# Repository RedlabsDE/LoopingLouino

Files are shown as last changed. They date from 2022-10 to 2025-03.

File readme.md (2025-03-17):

# LoopingLouino Project

find pictures and further description here: https://redlabs.de/blog/looping-louino/

## Repository Overview
- **documentation**
  - pictures of this project
- **firmware**
  - Arduino Project
- **hardware**
  - **KiCAD** Project Folder including schematic, PCB layout and BOM
  - **schematic** and fabrication layer drawing as PDF
  - **datasheet** of used components
  
## Hardware
- Order PCB: https://aisler.net/p/MKIYMUSK
- Assemble PCB (find BOM in \hardware\schematic)
- Rework PCB as described in the schematic

## Firmware

### Flash Arduino bootloader to your Atmega328

1. Open Atmel Studio (now Microchip Studio)
2. Start the Tool Manager. Connec your Atmel ISP to your PC and to the PCB (CON2, ISP 6-pin).
3. Select Tool and Device. Apply & Read.
4. "Fuses": Set Fuses (according to picture "Arduino Fuses.pg"). Program fuses to Device.
5. "Memories": For Flash, select the "optiboot_atmega328.hex" file. Program&Verify.

... find pictures and data here: \firmware\Arduino Bootloader

### Upload the LoopingLouino Fimrware 

Prepare:
- Get an USB/UART converter
- Connect the UART to the PCB (Pinheader P1, or use the Audio Jack J1)

Upload:
1. Open the firmware folder in VSCode
2. Install the "PlatformIO IDE" extension
3. Open the folder "180223-094129-pro16MHzatmega328" with the extension
4. Build and Upload the project.

... find other projects: https://redlabs.de/

### Debug the Firmware

In main.cpp set "#define DEBUG 1" to get serial debug information (8n1 19200)

### Adaptions in the Firware

According to the used Supply Voltage, set: #define SPEED_CORRECTION_FACTOR (main.h)

According to the number of LEDs used, set: #define NUM_LEDS (LEDcntrl.h)

## Mechanics

//TODO: add pictures

Open all screws (short / long)

remove black cable (between motor and batteries)
remove red cable (between switch and batteries)
remove battery clips

add new black cable to motor (20cm)
add new red cable to switch (20cm)

cut through plastic (battery holder)
drill through plastic frame (for DC Jack, Button and optional RC-Jack)

cut digital LED strip and attach 3-wire ribbon cable (20LEDs, or other number)

solder 3-wire LED cable to PCB
solder 2-Wire Motor-and-Switch cable to PCB

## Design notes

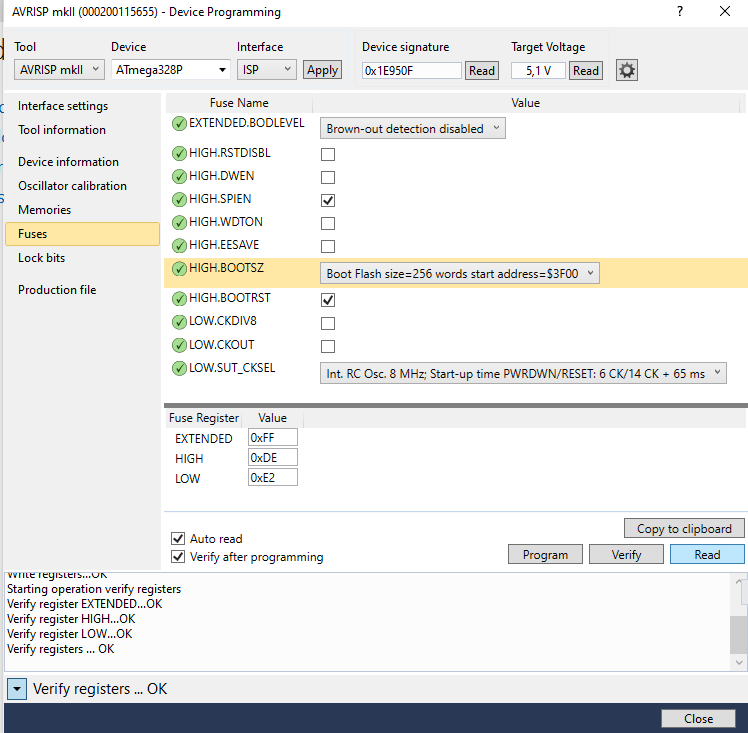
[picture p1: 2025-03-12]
firmware/Arduino Bootloader/Arduino Fuses.png

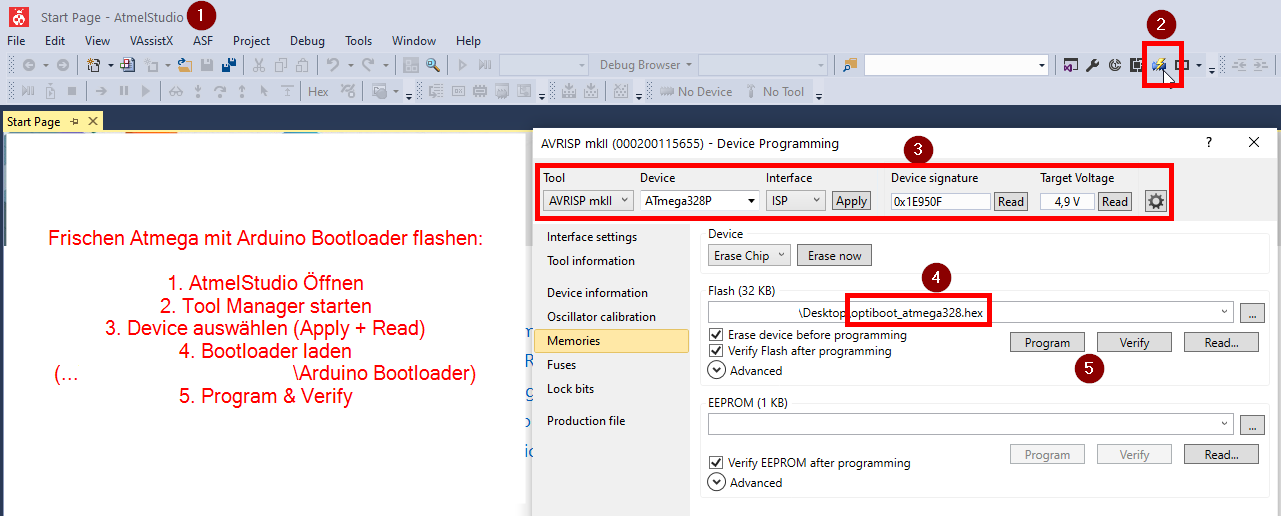
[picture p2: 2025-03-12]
firmware/Arduino Bootloader/Arduino Bootloader flashen.png

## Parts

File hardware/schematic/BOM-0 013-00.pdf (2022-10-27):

redlabs.de | BOM 013/00 | LoopingLouino
| | Total parts: | 50
v C | 22u | C_1206 | 1
C14 | 22u
v C | 100p | C_0603 | 1
C12 | 100p
v C | 1n | C_0603 | 4
C1 | 1n
C2 | 1n
C3 | 1n/200V
C4 | 1n
v C | 100n | C_0603 | 9
C5 | 100n
C6 | 100n
C7 | 100n
C8 | 100n
C10 | 100n/25V
C11 | 100n
C17 | 100n
C18 | 100n
C19 | 100n
v C | 1u/25V | C_0805 | 2
C9 | 1u/25V
C16 | 1u/25V
v R | 2R2 | R_0805 | 1
R17 | 2R2
v R | 1k | R_0603 | 3
R3 | 1k
R21 | 1k
R22 | 1k
v R | 4k7 | R_0603 | 2
R9 | 4k7
R10 | 4k7
v R | 7k5 | R_0603 | 1
R16 | 7k5
v R | 10k | R_0603 | 6
R1 | 10k
R13 | 10k
R14 | 10k
R18 | 10k
R19 | 10k
R20 | 10k
v R | 22k | R_0603 | 3
R2 | 22k
R23 | 22k
R24 | 22k
v R | 39k | R_0603 | 1
R15 | 39k
v R | 100k | R_0603 | 3

R7 | 100k
R8 | 100k
R12 | 100k
v D | SK34A | D_SMA | 2
D1 | SK34A
D2 | SK34A
v L | 10uH | D_SMA | 1
L1 | 10uH (HPI0530-100)
v Q | BCR141 | SOT-23 | 2
Q4 | BCR141
Q5 | BCR141
v IC | | | 3
IC1 | ATMEGA328P-A | TQFP-32_7x7mm_Pitch0.8mm
U2 | MP1584 | SO8N
U3 | ZXMHC6A07T8-2 | SOT-223-8
v SW | Switches | | 2
SW1 | SW_PUSH | SW_Tactile_SPST_Angled_PTS645Vx83-2LFS
SW2 | SW_PUSH | SMD_pushbutton_4x6mm
v CON | Connectors | | 3
J1 | JACK_4P | Klinkenbuchse-1503-13VP3
CON1 | BARREL_JACK_reduced | BARREL_JACK_reduced
CON2 | AVR-ISP-6 | MicroMatch_2x3_SMD
v P | Pin Array
P2 | CONN_01X03 | PIN_ARRAY_3x1_drill_0.8mm
P3 | CONN_01X02 | JST_XH2P_oval_pads
v P | Not Populated | | 5
R11 | 33R | R_0603
R4 | 0R | R_0603
R5 | 10k | R_0603
R25 | 1k | R_0603
Q1 | PMV250 | SOT-23

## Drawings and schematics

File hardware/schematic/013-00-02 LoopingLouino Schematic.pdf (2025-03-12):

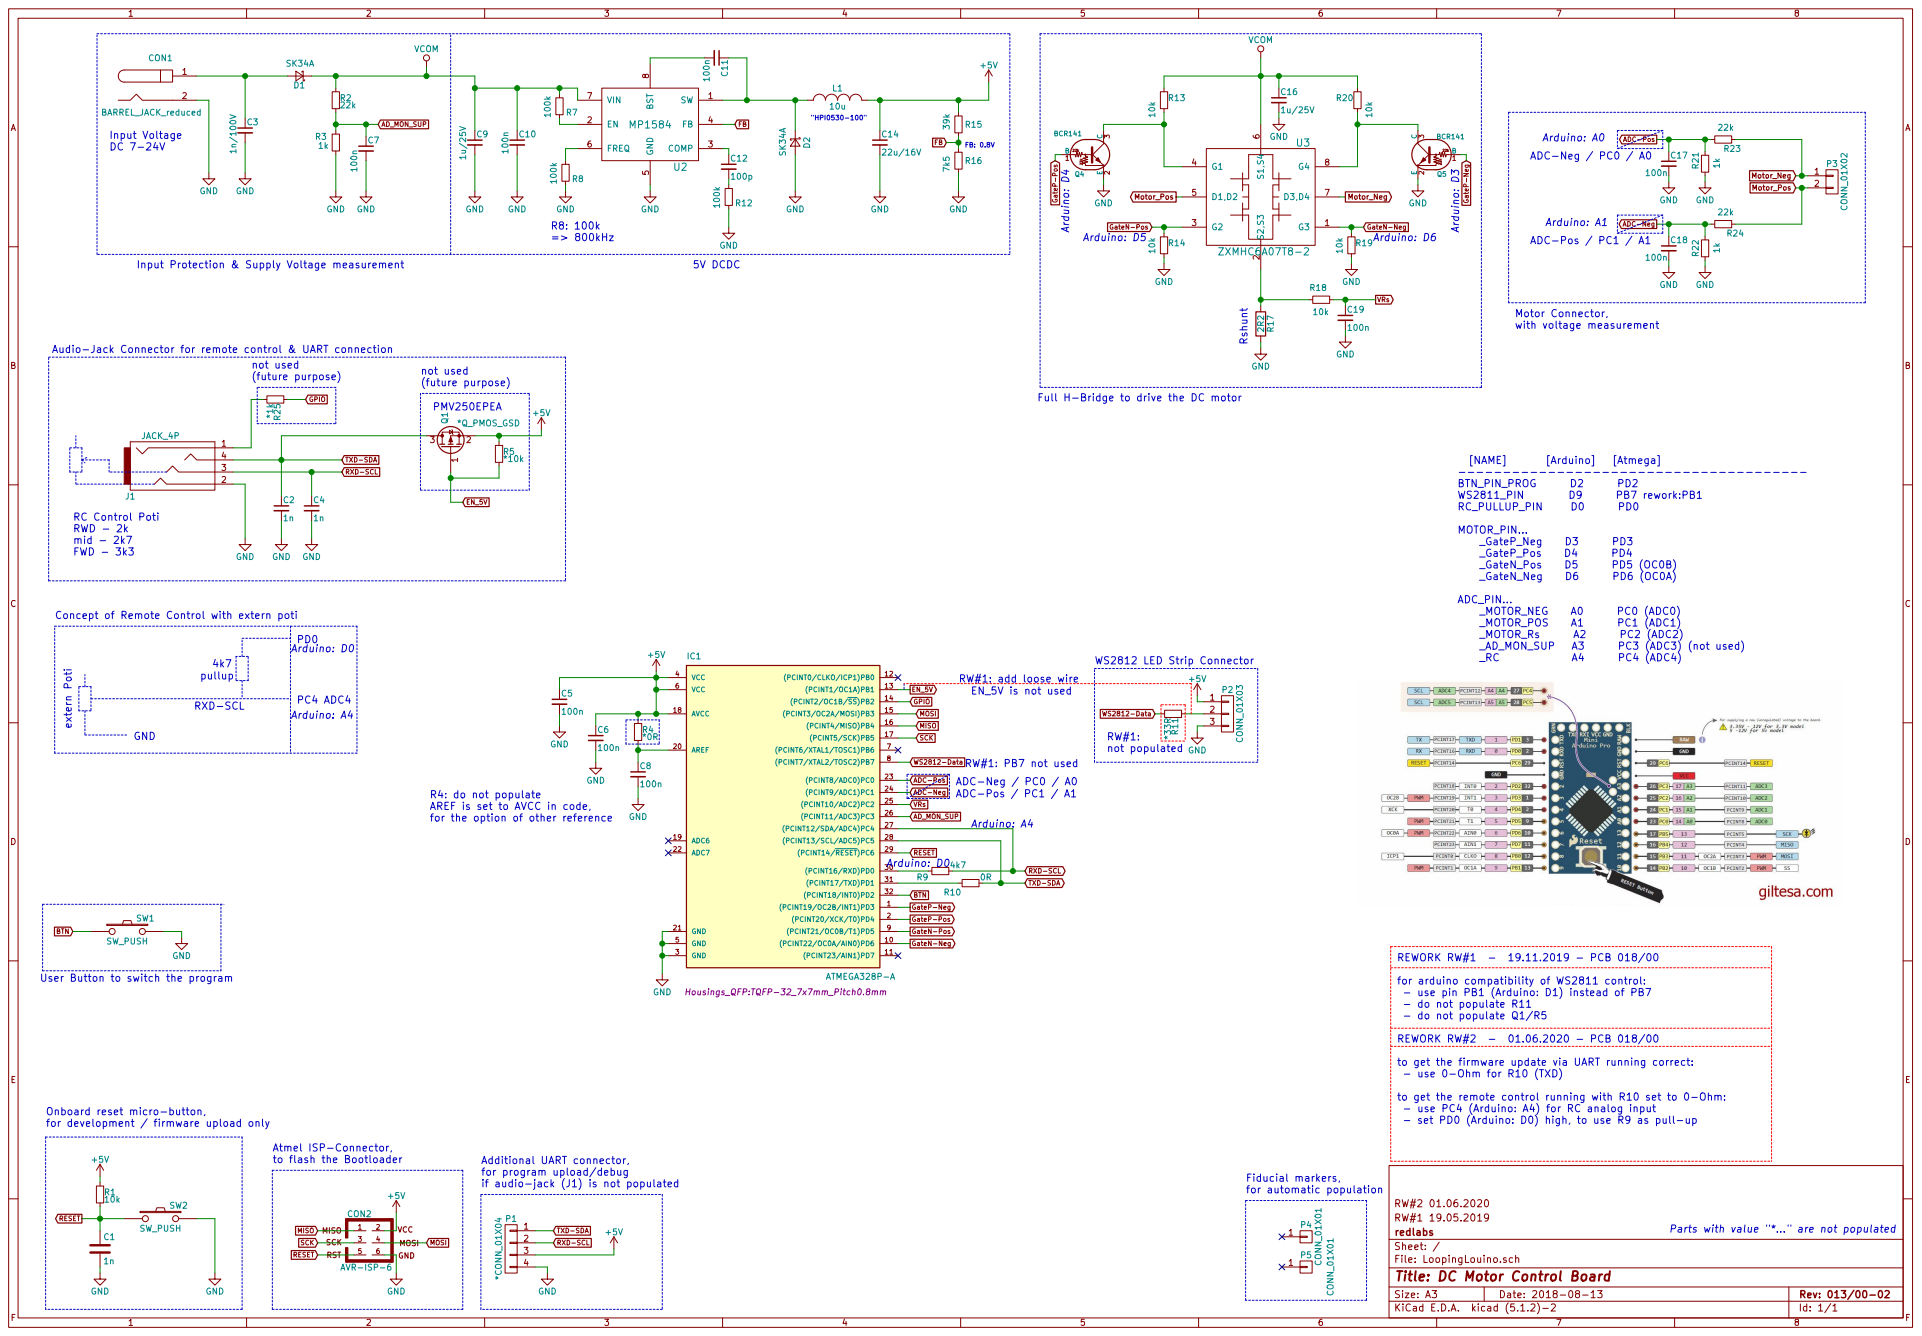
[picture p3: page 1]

Audio-Jack Connector for remote control & UART connection
Concept of Remote Control with extern poti not used

Full H-Bridge to drive the DC motor

RXD-SCL TXD-SDA

R4: do not populate
AREF is set to AVCC in code,
for the option of other reference

BTN
GateN-Pos GateN-Neg GateP-Pos GateP-Neg

User Button to switch the program

for arduino compatibility of WS2811 control:
- use pin PB1 (Arduino: D1) instead of PB7
- do not populate R11
- do not populate Q1/R5

to get the firmware update via UART running correct:
- use 0-Ohm for R10 (TXD)

to get the remote control running with R10 set to 0-Ohm:
- use PC4 (Arduino: A4) for RC analog input
- set PD0 (Arduino: D0) high, to use R9 as pull-up

Onboard reset micro-button,
for development / firmware upload only

Additional UART connector,
for program upload/debug
if audio-jack (J1) is not populated

File: LoopingLouino.sch Sheet: / redlabs RW#1 19.05.2019 RW#2 01.06.2020

Parts with value "*..." are not populated

Id: 1/1 Title: DC Motor Control Board

GND

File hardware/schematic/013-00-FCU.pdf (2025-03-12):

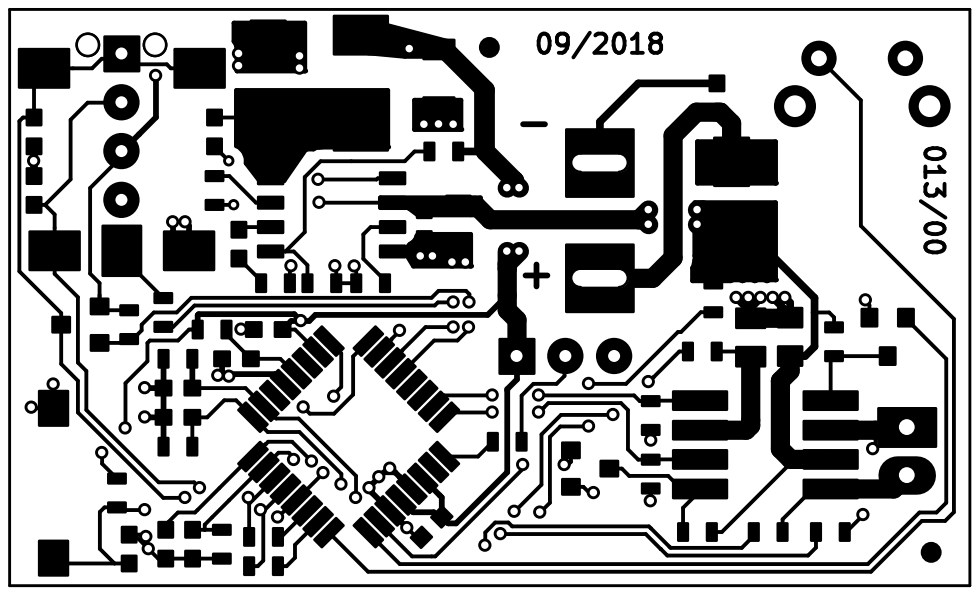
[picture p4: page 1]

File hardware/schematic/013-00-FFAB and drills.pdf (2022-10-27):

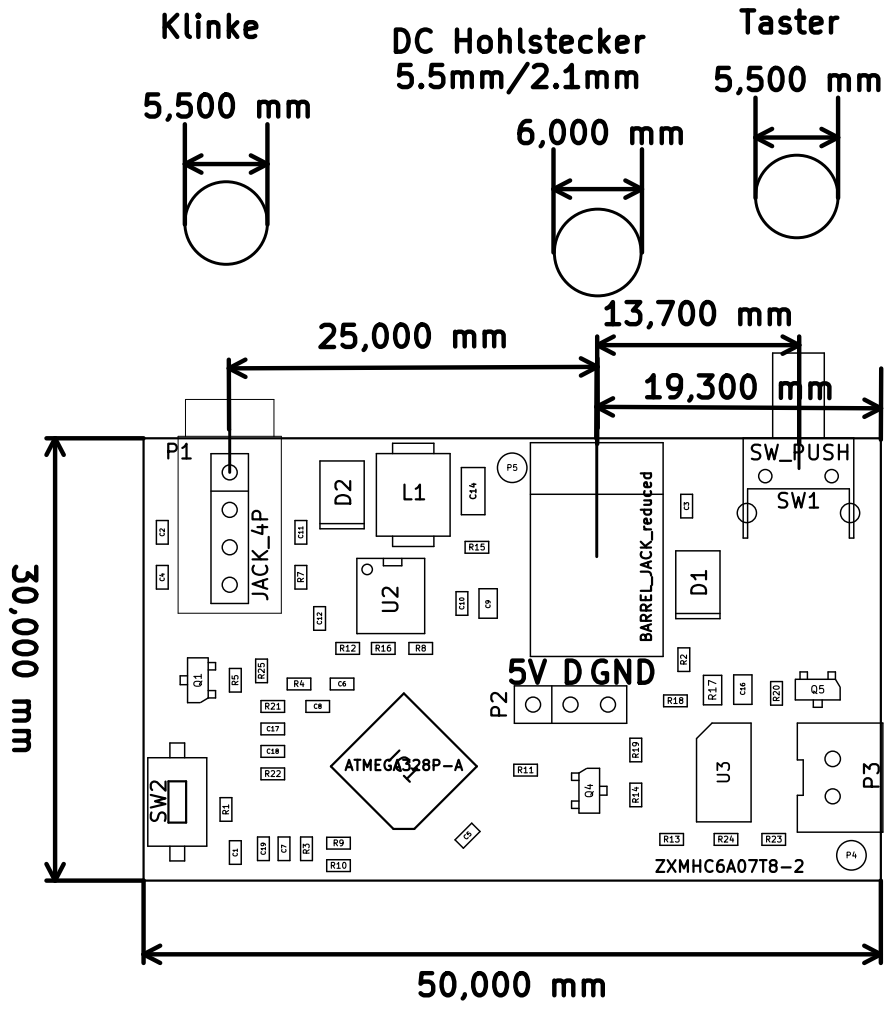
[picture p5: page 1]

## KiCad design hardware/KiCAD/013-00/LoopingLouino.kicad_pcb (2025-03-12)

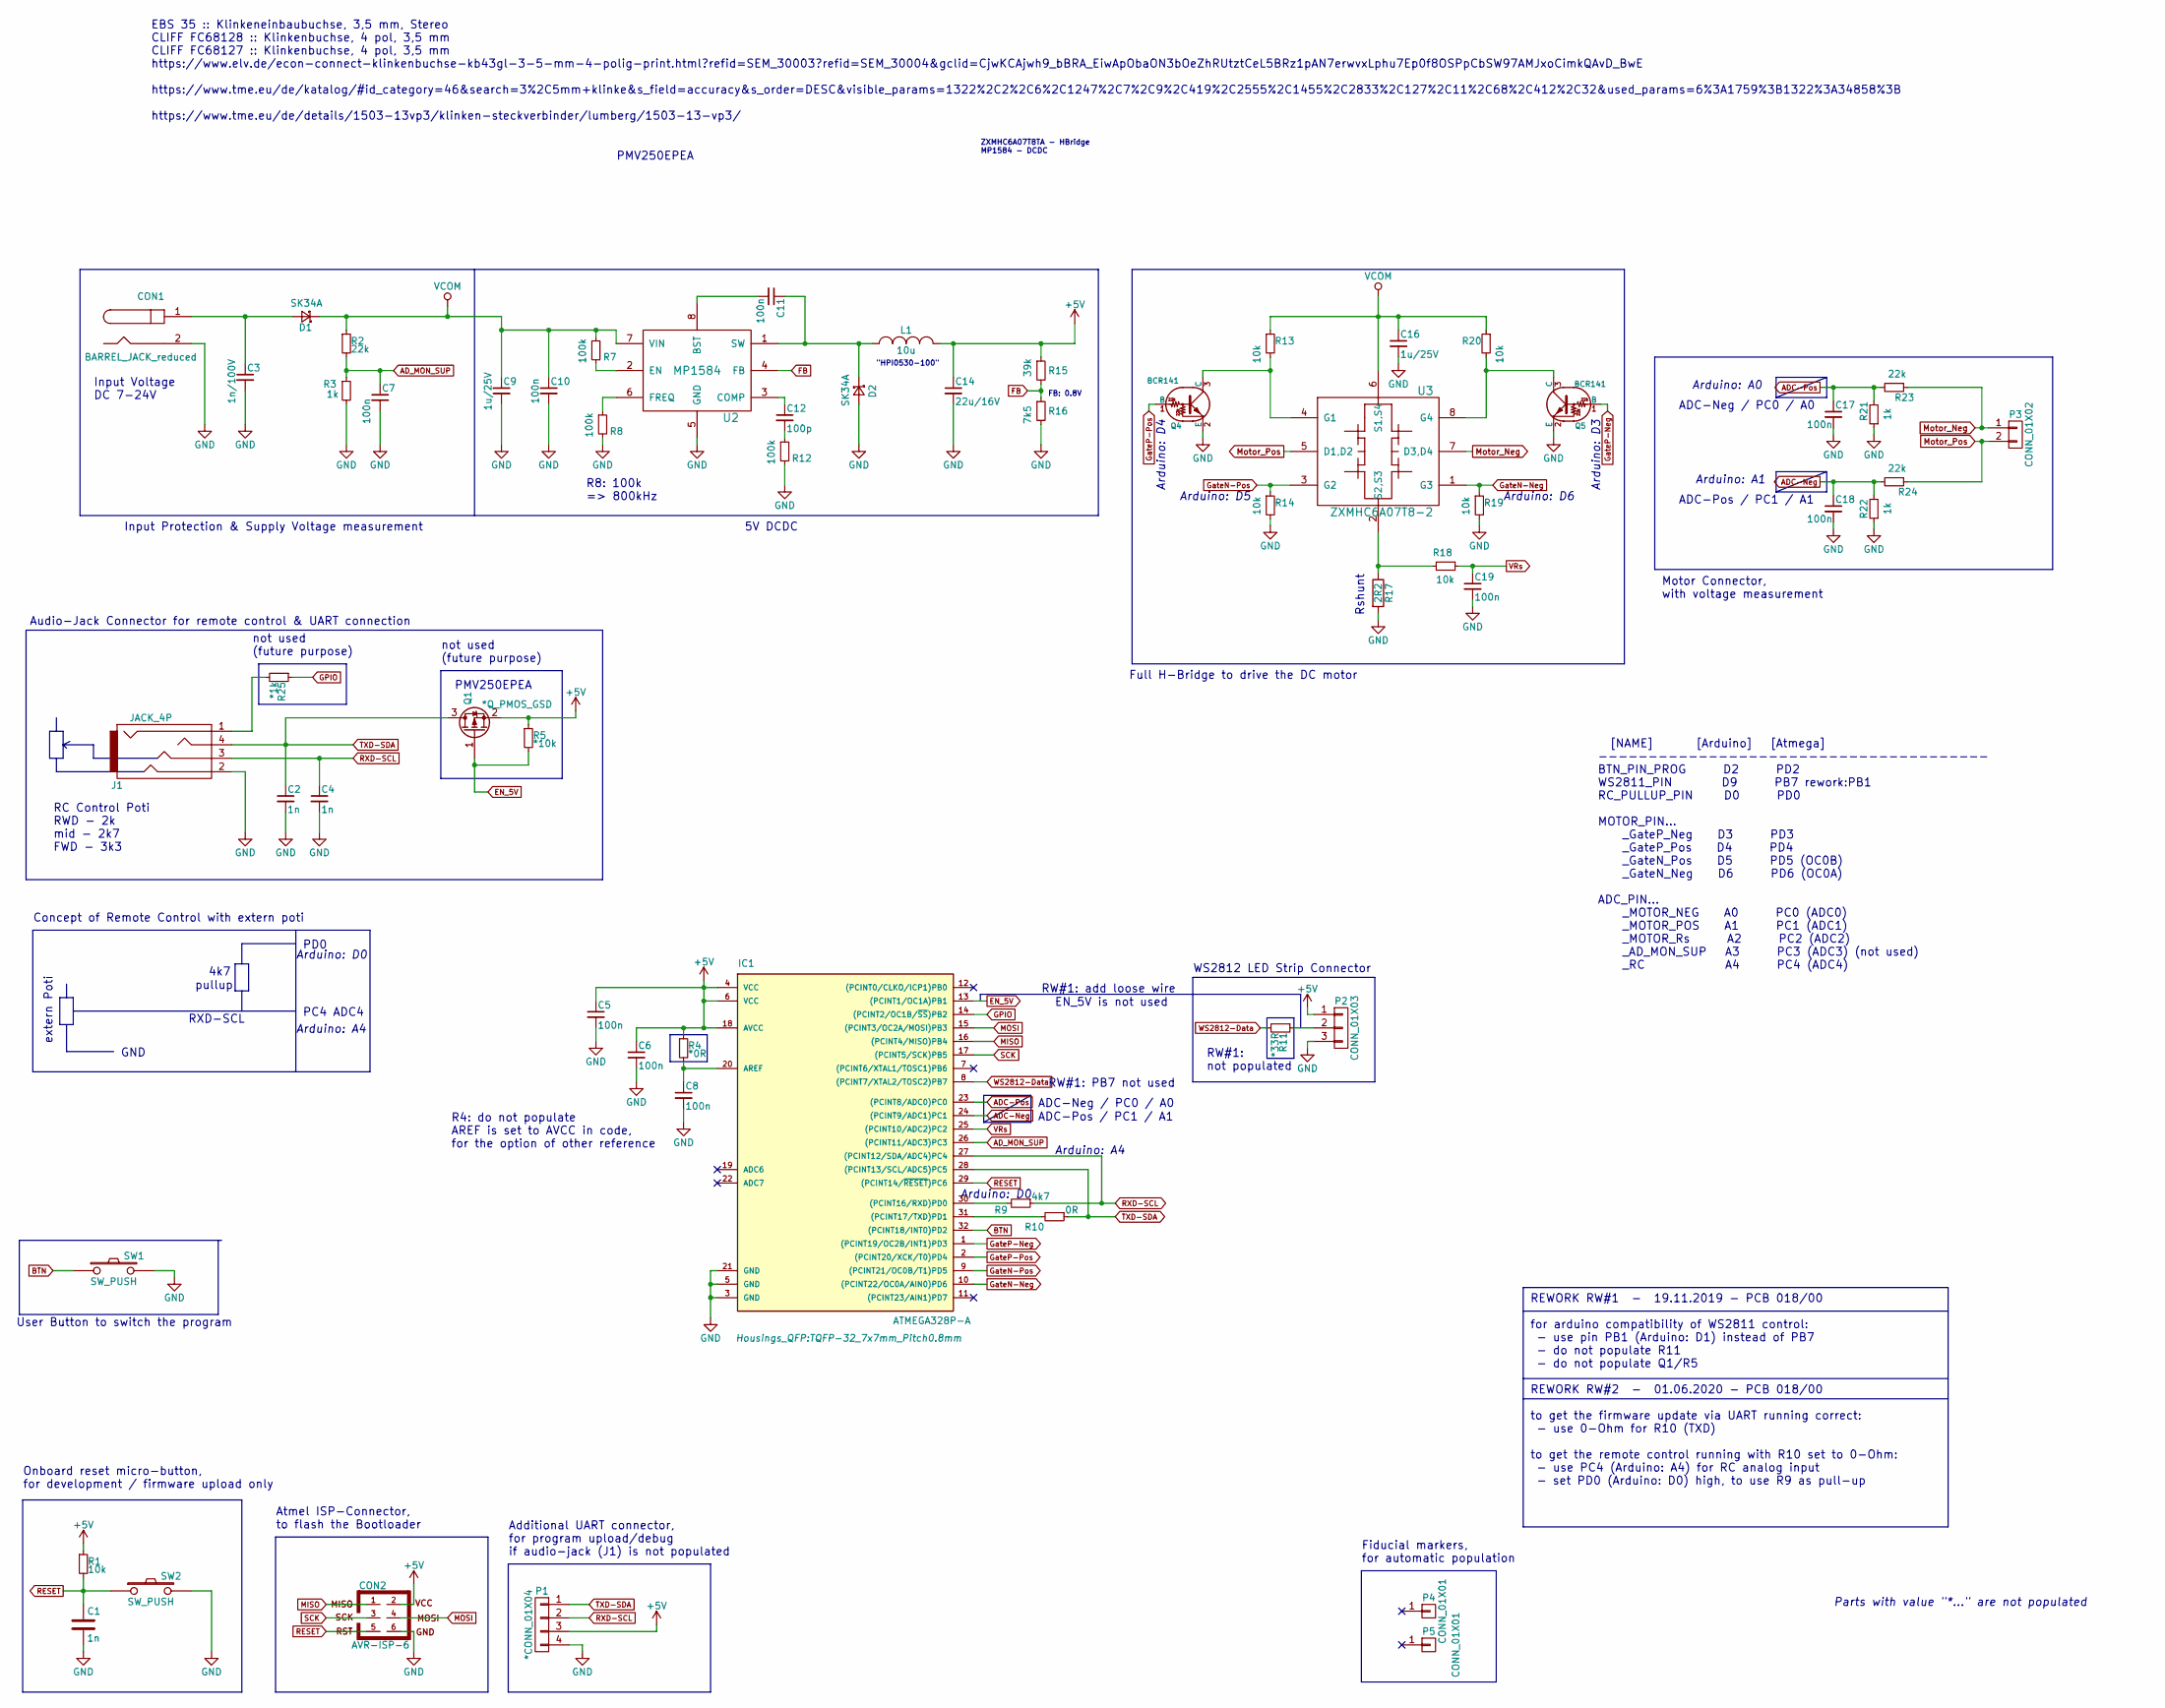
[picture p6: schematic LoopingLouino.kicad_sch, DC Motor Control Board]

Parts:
C1, C2, C4: 1n; C_0603
C3: 1n/100V; C_0603
C5, C6, C7, C8, C10, C11, C17, C18, C19: 100n; C_0603
C9, C16: 1u/25V; C_0805
C12: 100p; C_0603
C14: 22u/16V; C_1206
CON1: BARREL_JACK_reduced
CON2: AVR-ISP-6; MicroMatch_2x3_SMD
D1, D2: SK34A; D_SMA
IC1: ATMEGA328P-A; TQFP-32_7x7mm_Pitch0.8mm
J1: JACK_4P; Klinkenbuchse-1503-13VP3
L1: 10u; Inductor_HPI0530-xxx
P1: *CONN_01X04; PIN_ARRAY_4x1_drill_0.8mm
P2: CONN_01X03; PIN_ARRAY_3x1_drill_0.8mm
P3: CONN_01X02; JST_XH2P_oval_pads
P4, P5: CONN_01X01; Fiducial_1mm_Dia_2mm_Outer
Q1: *Q_PMOS_GSD; SOT-23-RL
Q4, Q5: BCR141; SOT-23-RL
R1, R13, R14, R18, R19, R20: 10k; R_0603
R2, R23, R24: 22k; R_0603
R3, R21, R22: 1k; R_0603
R4: *0R; R_0603
R5: *10k; R_0603
R7, R8, R12: 100k; R_0603
R9: 4k7; R_0603
R10: 0R; R_0603
R11: *33R; R_0603
R15: 39k; R_0603
R16: 7k5; R_0603
R17: 2R2; R_0805_redlabs
R25: *1k; R_0603
SW1: SW_PUSH; SW_Tactile_SPST_Angled_PTS645Vx83-2LFS
SW2: SW_PUSH; SMD_pushbutton_4x6mm
U2: MP1584; SO8N-RL
U3: ZXMHC6A07T8-2; SOT-223-8

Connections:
+5V: C5.1, C6.1, C14.1, CON2.2, IC1.4 (VCC), IC1.6 (VCC), IC1.18 (AVCC), L1.2, P1.3, P2.1, Q1.2 (S), R1.1, R4.1, R5.1, R15.1
ADC-Neg: C18.1, IC1.24 ((PCINT9/ADC1)PC1), R22.2, R24.2
ADC-Pos: C17.1, IC1.23 ((PCINT8/ADC0)PC0), R21.2, R23.2
AD_MON_SUP: C7.1, IC1.26 ((PCINT11/ADC3)PC3), R2.2, R3.1
BTN: IC1.32 ((PCINT18/INT0)PD2), SW1.1
EN_5V: IC1.13 ((PCINT1/OC1A)PB1), Q1.1 (G), R5.2
FB: R15.2, R16.1, U2.4 (FB)
GND: C1.2, C2.2, C3.2, C4.2, C5.2, C6.2, C7.2, C8.2, C9.2, C10.2, C14.2, C16.2, C17.2, C18.2, C19.2, CON1.2, CON2.6, D2.2 (A), IC1.3 (GND), IC1.5 (GND), IC1.21 (GND), J1.2, P1.4, P2.3, Q4.2 (E), Q5.2 (E), R3.2, R8.2, R12.2, R14.2, R16.2, R17.2, R19.2, R21.1, R22.1, SW1.2, SW2.2, U2.5 (GND)
GPIO: IC1.14 ((PCINT2/OC1B/~SS)PB2), R25.1
GateN-Neg: IC1.10 ((PCINT22/OC0A/AIN0)PD6), R19.1, U3.1 (G3)
GateN-Pos: IC1.9 ((PCINT21/OC0B/T1)PD5), R14.1, U3.3 (G2)
GateP-Neg: IC1.1 ((PCINT19/OC2B/INT1)PD3), Q5.1 (B)
GateP-Pos: IC1.2 ((PCINT20/XCK/T0)PD4), Q4.1 (B)
MISO: CON2.1, IC1.16 ((PCINT4/MISO)PB4)
MOSI: CON2.4, IC1.15 ((PCINT3/OC2A/MOSI)PB3)
Motor_Neg: P3.1, R23.1, U3.7 (D3,D4)
Motor_Pos: P3.2, R24.1, U3.5 (D1,D2)
unnamed: C3.1, CON1.1, D1.2 (A)
unnamed: C8.1, IC1.20 (AREF), R4.2
unnamed: C11.1, D2.1 (K), L1.1, U2.1 (SW)
unnamed: C11.2, U2.8 (BST)
unnamed: C12.1, U2.3 (COMP)
unnamed: C12.2, R12.1
unnamed: IC1.30 ((PCINT16/RXD)PD0), R9.2
unnamed: IC1.31 ((PCINT17/TXD)PD1), R10.2
unnamed: J1.1, R25.2
unnamed: P2.2, R11.1
unnamed: Q4.3 (C), R13.2, U3.4 (G1)
unnamed: Q5.3 (C), R20.2, U3.8 (G4)
unnamed: R7.2, U2.2 (EN)
unnamed: R8.1, U2.6 (FREQ)
unnamed: R17.1, R18.2, U3.2 (S2,S3)
RESET: C1.1, CON2.5, IC1.29 ((PCINT14/~RESET)PC6), R1.2, SW2.1
RXD-SCL: C4.1, IC1.27 ((PCINT12/SDA/ADC4)PC4), J1.3, P1.2, R9.1
SCK: CON2.3, IC1.17 ((PCINT5/SCK)PB5)
TXD-SDA: C2.1, IC1.28 ((PCINT13/SCL/ADC5)PC5), J1.4, P1.1, Q1.3 (D), R10.1
VCOM: C9.1, C10.1, C16.1, D1.1 (K), R2.1, R7.1, R13.1, R20.1, U2.7 (VIN), U3.6 (S1,S4)
VRs: C19.1, IC1.25 ((PCINT10/ADC2)PC2), R18.1
WS2812-Data: IC1.8 ((PCINT7/XTAL2/TOSC2)PB7), R11.2

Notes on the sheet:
PMV250EPEA
Arduino: D6
ADC-Pos / PC1 / A1
ADC-Neg / PC0 / A0
R4: do not populate AREF is set to AVCC in code, for the option of other reference
Motor Connector, with voltage measurement
Parts with value "*..." are not populated
Arduino: D4
GND
Arduino: D0
Additional UART connector, for program upload/debug if audio-jack (J1) is not populated
"HPI0530-100"
RW#1: PB7 not used
User Button to switch the program
Rshunt
Onboard reset micro-button, for development / firmware upload only
Input Protection & Supply Voltage measurement
Atmel ISP-Connector, to flash the Bootloader
FB: 0.8V
REWORK RW#1 - 19.11.2019 - PCB 018/00 for arduino compatibility of WS2811 control: - use pin PB1 (Arduino: D1) instead of PB7 - do not populate R11 - do not populate Q1/R5 REWORK RW#2 - 01.06.2020 - PCB 018/00 to get the firmware update via UART running correct: - use 0-Ohm for R10 (TXD) to get the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
WS2812 LED Strip Connector
pullup
Arduino: A4
RC Control Poti RWD - 2k mid - 2k7 FWD - 3k3
EBS 35 :: Klinkeneinbaubuchse, 3,5 mm, Stereo CLIFF FC68128 :: Klinkenbuchse, 4 pol, 3,5 mm CLIFF FC68127 :: Klinkenbuchse, 4 pol, 3,5 mm https://www.elv.de/econ-connect-klinkenbuchse-kb43gl-3-5-mm-4-polig-print.html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…
not used (future purpose)
4k7
RW#1: not populated
Audio-Jack Connector for remote control & UART connection
RXD-SCL
[NAME] [Arduino] [Atmega] --------------------------------------- BTN_PIN_PROG D2 PD2 WS2811_PIN D9 PB7 rework:PB1 RC_PULLUP_PIN D0 PD0 MOTOR_PIN... _GateP_Neg D3 PD3 _GateP_Pos D4 PD4 _GateN_Pos D5 PD5 (OC0B) _GateN_Neg D6 PD6 (OC0A) ADC_PIN... _MOTOR_NEG A0 PC0 (ADC0) _MOTOR_POS A1 PC1 (ADC1) _MO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
EN_5V is not used
Arduino: D3
Arduino: D5
R8: 100k => 800kHz
Arduino: A0
Full H-Bridge to drive the DC motor
extern Poti
RW#1: add loose wire
Fiducial markers, for automatic population

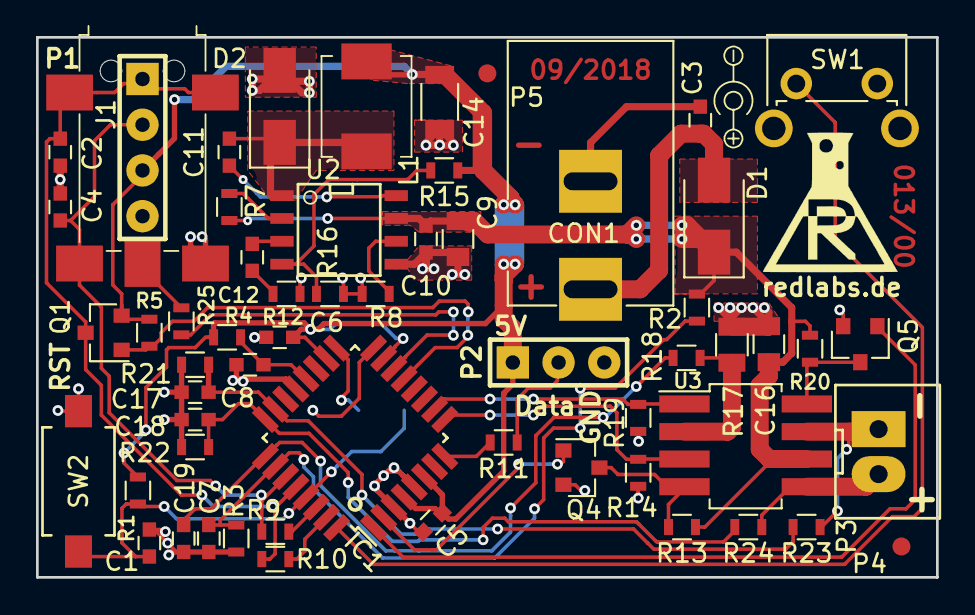
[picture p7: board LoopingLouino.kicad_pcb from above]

Board: 2 copper layers, 50.0 x 30.0 mm, 60 parts (1 on the bottom side), 39 nets.

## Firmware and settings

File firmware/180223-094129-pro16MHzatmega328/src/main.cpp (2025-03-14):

/*
 * LoopingLoui v6
 *
 * Created: 17.07.2018
 *  Author: Julian Hauser
 *  www.redlabs.de
 */

/*
 * Board: "Arduino Pro or Pro Mini"
 * Prozessor: "ATmega328 5V 16MHz"
 * Programmer: "AVR ISP"
 */

 //redlabs PCB 013-00
 //Vin DC 7.5V / 12V (set correct SPEED_CORRECTION_FACTOR)

/*
v00
v01
v02
23.02.2018  v03   switch to Atom IDE
08.03.2018  v06   switch to MOTOR_L9110 and Arduino Mini Pro (013-xx breadboard)
17.03.2018  v07   WS2811 control corrected, new engineControl2()
19.03.2018  v08   tidy up code, add LEDcntrl, capacitor added at "raw" pin -> no resets at change of direction
20.03.2018  R1.0  decission: Vin=7.5V, ramp up/down improved
25.03.2018  v1.1  start to add analog RC-Control
26.03.2018  v1.2  RC-control
26.03.2018  R1.3  RC control implemented correct, tidy up code, [Osterwidum '18 release]

08.01.2019  v1.4  switch to PCB 013/00: pin mapping changed / use of MOTOR_HBRIDGE / ON/OFF switch in series with motor
18.11.2019        checkStartSwitch2 implemented correct
19.11.2019        LEDs control done / RC control done
21.11.2019 R1.6   Release (Felix&Nadja)
02.12.2019 R1.7   Release (Felix&Nadja), RC control adapted to new (black) RC control
09.06.2020 1.8    Change RC-pin to PC4/ADC4/RXD (ADC5 seems to be damaged), also changed pinning in blue RC-Control to mid-pin, TODO: correct control of 4 LEDs (instead of 11)
15.06.2020 R1.9   Running Version - Change to 12V supply/ control of 4 LEDs fixed / change random speed change time from 3 to 5 sec / add ADC lowpass filter to Remote control

12.03.2025        Add Comments & Tidy up. Use 7.5V supply voltage. Use 20 LEDs.
  
TODO: extra program with LED show - or LED show after some time if motor is not running
*/

#define MOTOR_L9110   0 //obsolete
#define MOTOR_L293    0 //obsolete
#define MOTOR_HBRIDGE 1 //use discrete MOSFET H-Bridge

#define LOOPDELAY_MS      10
#define DELAY_CORRECTION  64 //TIMER0 is changed to set the motor PWM -> affects arduino delay() / workaround: delay( time_ms *DELAY_CORRECTION);

#define DEBUG 0

#include "main.h"
#include "LEDcntrl.h"

///////////////////////////////////////////////////////////////////////////////
//This function will be called when PROG Button is pressed
void ISRbtnPROG()
{
  sem_nextProgram = 1; //button press event will be processed in main loop
  delay(10*DELAY_CORRECTION);
}
///////////////////////////////////////////////////////////////////////////////
//setup
void setup()
{
  #if DEBUG
    Serial.begin(19200);
  #endif

//user button "program selection"
  pinMode(BTN_PIN_PROG, INPUT);
  digitalWrite(BTN_PIN_PROG, HIGH); //enable intern pullup
  attachInterrupt(digitalPinToInterrupt(BTN_PIN_PROG), ISRbtnPROG, FALLING);

//RC Control onboard pullup pin
  pinMode(RC_PULLUP_PIN, OUTPUT); //enable internal pullup
  digitalWrite(RC_PULLUP_PIN, HIGH); //enable intern pullup

//WS2811 OUTPUT
  pinMode(WS2811_PIN, OUTPUT);

//Motor control
  #if MOTOR_L9110
    pinMode(MOTOR_PIN_DIR, OUTPUT);
    pinMode(MOTOR_PIN_PWM, OUTPUT);
    digitalWrite(MOTOR_PIN_DIR, LOW);
    digitalWrite(MOTOR_PIN_PWM, LOW);
  #endif

  #if MOTOR_HBRIDGE
    pinMode(MOTOR_PIN_GateP_Neg, OUTPUT);
    pinMode(MOTOR_PIN_GateP_Pos, OUTPUT);
    pinMode(MOTOR_PIN_GateN_Pos, OUTPUT); //PWM
    pinMode(MOTOR_PIN_GateN_Neg, OUTPUT); //PWM

    digitalWrite(MOTOR_PIN_GateP_Neg, LOW);
    digitalWrite(MOTOR_PIN_GateP_Pos, LOW);
    digitalWrite(MOTOR_PIN_GateN_Pos, LOW);
    digitalWrite(MOTOR_PIN_GateN_Neg, LOW);

  #endif

  //Set Motor PWM frequency, (default: 490 Hz), //this changes the delay() time!!!!
  setPwmFrequency(MOTOR_PIN_GateN_Pos,1); //set PWM freq to 32kHz (31250/1 Hz)
  setPwmFrequency(MOTOR_PIN_GateN_Neg,1); //set PWM freq to 32kHz (31250/1 Hz)

//watchdog enable
  //wdt_enable(WDTO_2S);
  //wdt_reset();
  //wdt_disable();

//WS2812 start:
  strip.begin();
  strip.show(); // Initialize all pixels to 'off'
  strip.clear();
  rainbow(5*DELAY_CORRECTION);  //start up LED show

  #if DEBUG
    Serial.println("xxxxxxxxxxxxxxxxxxxxxxx");
    Serial.println("redlabs Looping Loui V6");
    Serial.println("DEBUG enabled");
  #endif

  sem_nextProgram = 0;
  sem_starStop = 1;
}

///////////////////////////////////////////////////////////////////////////////
//main loop
void loop()
{
  ///////////////////////////////////////////////////////////////////////////////
  //main loop count (dt: 10ms)
  loopCount++;
  if(loopCount>1000) //start again at 0 after ~10 sec
  {
    loopCount = 0;
    #if DEBUG
      debugDiagnose();
    #endif
  }
  //wdt_reset();

  ///////////////////////////////////////////////////////////////////////////////
  //if "PROG" button was pressed: switch to next program
  if(sem_nextProgram)
    incrementProgram();
  ///////////////////////////////////////////////////////////////////////////////
  //Check status of main LoopingLoui switch & set stat_current to RUN/PAUSE
  checkStartSwitch();
  ///////////////////////////////////////////////////////////////////////////////
  //execute RUN / PAUSE mode
  if(stat_current == STAT_RUN) //while stauts = RUN, execute current program
  {
    executeProgram();
  }
  else if(stat_current == STAT_PAUSE) //if status = "PAUSE", pause current program
  {
    MOTOR_speed_new = 0;
    MOTOR_direction_new = STOP;
  }
  //////////////////////////////////////////////////////////////////////////////
  //set motor speed & direction
  engineControl();
  //show current program/state with LEDs
  LEDshowProgram();
  //main loop delay
  delay(LOOPDELAY_MS*DELAY_CORRECTION); //10ms loop
}


///////////////////////////////////////////////////////////////////////////////
//if PROGRAM button is pushed, go to next program
void incrementProgram()
{
  prog_current++; //increment progam number

  if(prog_current>MAX_PROGRAM) //if max program reached, go to program 1
  {
    prog_current=1;
    MOTOR_speed = MINSPEED; //set speed to low value, to start again the "PROG_SPEEDUP"
  }

  #if DEBUG
    Serial.println("next program selected: ");
    Serial.print(prog_current);
  #endif

  delay(300*DELAY_CORRECTION); //debounce
  sem_nextProgram = 0; //reset the button press semaphor
}


///////////////////////////////////////////////////////////////////////////////
//check status of main LoopinLoui I/O switch and set status to RUN/PAUSE
// I/O switch is in series with motor
/*
// Start switch decission table:
if (Motor == stopped) set "GateP-Pos" active
  switch off: ADC-Neg = 0V
  switch on:  ADC-Neg = VCOM
if (Motor == running)
  if (direction == forward) GateP-Pos is active
    switch off: ADC-Neg = 0V
    switch on: ADC-Neg > 0V
  if (direction == backward) GateP-Neg is active
    switch off: ADC-Pos = 0V
    switch on: ADC-Pos > 0V
*/
void checkStartSwitch()
{
  static char switchIsOn = 0;
  ///////////////////////////////////////////////////////////////////////////////
  //get analog inputs - voltage at motor connection or motor current
  Motor_Neg_ADC = analogRead(ADC_PIN_MOTOR_NEG);
  Motor_Pos_ADC = analogRead(ADC_PIN_MOTOR_POS);

  if(currentSenseDeactivate) //motor current sense is deactivated for a short time when the switch is turned on - to give the motor current time to rise
  {
    Motor_Rs_ADC_FILTER = MOTOR_CURRENT_ADC_OFF_LEVEL + 1;
    currentSenseDeactivate--;
  }
  else
  {
    Motor_Rs_ADC  = analogRead(ADC_PIN_MOTOR_Rs); //measurement of motor current over shunt resistor
    Motor_Rs_ADC_FILTER = lowPassAveraging_Rs(Motor_Rs_ADC); //apply filter
  }

  ////////////////////////////////////////////////////
  //check voltage at motor connection depending on run mode
  if(MOTOR_direction == STOP)
  {
    if(Motor_Neg_ADC < MOTOR_VOLTAGE_ADC_OFF_LEVEL) //switch == OFF
    {
      switchIsOn = 0;
    }
    else //switch == just turned ON
    {
      switchIsOn = 1;
      currentSenseDeactivate = CURRENT_SENSE_DEACTIVATE_TIME;
    }
  }
  else if ( (MOTOR_direction == FWD) || (MOTOR_direction == RWD) )
  {
    if(Motor_Rs_ADC_FILTER < MOTOR_CURRENT_ADC_OFF_LEVEL) //no motor current -> switch == OFF
    {
      switchIsOn = 0;
    }
    else //switch = ON
    {
      switchIsOn = 1;
    }
  }
  ////////////////////////////////////////////////////
  //set status according to switch position
  if(switchIsOn == 0 ) //switch == OFF
  {
    stat_current = STAT_PAUSE;
    if(sem_starStop == 1)
    {
      #if DEBUG
        Serial.println("status: pause");
      #endif
    }
    sem_starStop = 0;
  }
  else //switch == ON
  {
    stat_current = STAT_RUN;
    if(sem_starStop == 0)
    {
      #if DEBUG
        Serial.println("status: run");
      #endif
    }
    sem_starStop = 1;
  }

}

///////////////////////////////////////////////////////////////////////////////
//goto selected program
void executeProgram()
{
  switch (prog_current)
  {
    ////////////////////////////////////////////////////
    //normal motor speed,chaser lights
    case PROG_NORMAL:

        MOTOR_speed_new = NORMSPEED;
        MOTOR_direction_new = FWD;
    break;
    ////////////////////////////////////////////////////
    //incresase motor speed with time
    case PROG_SPEEDUP:

        if(MOTOR_speed_new < MINSPEED)
          MOTOR_speed_new = MINSPEED;

        if(MOTOR_speed_new < MAXSPEED) //while max speed is not reached, increment speed
        {
          if(!(loopCount % (500/LOOPDELAY_MS))) //increase speed every 500 ms
          {
            #if DEBUG
              Serial.println("speed up");
            #endif
            MOTOR_speed_new += SPEEDUP;
            MOTOR_direction_new = FWD;
          }
        }
    break;
    ////////////////////////////////////////////////////
    //random change of speed and direction - redlabs best choice :)
    case PROG_CRACY:

        if(MOTOR_speed_new < MINSPEED)
        {
          MOTOR_speed_new = MINSPEED;
          MOTOR_direction_new = FWD;
        }

        if(!(loopCount %  (5000/LOOPDELAY_MS) )) //change speed/direction every 5 seconds
        {
          unsigned char direction = 0;

          MOTOR_speed_new = random(MINSPEED,MAXSPEED);
          //MOTOR_speed_new = rand()%175+70; //get random speed value in range (70:255)
          direction = random(1,100);
          //direction = rand()%100+1; //get random direction value in range (1:100)

          if(direction>15) //85% chance to go forward
            MOTOR_direction_new = FWD;
          else
            MOTOR_direction_new = RWD;
        }
    break;
    ////////////////////////////////////////////////////
    //go forward with max speed
    case PROG_MAXSPEED:

        MOTOR_direction_new = FWD;
        MOTOR_speed_new = MAXSPEED;
    break;
    ////////////////////////////////////////////////////
    //use analog input as remote control
    case PROG_RC:

        if(!(loopCount %  (50/LOOPDELAY_MS) )) //read remote control every 50 milli seconds
        {
          //RC_ADC = analogRead(ADC_PIN_RC);
          RC_ADC = lowPassAveraging_RC(analogRead(ADC_PIN_RC)); //apply filter

          #if DEBUG
            Serial.println("ADC: ");
            Serial.print(RC_ADC);
          #endif
          RemoteControl (RC_ADC);
        }
    break;
    ////////////////////////////////////////////////////
    //should not appear
    default:
      //trigger watchdog to reset controller
    break;
  }
}

///////////////////////////////////////////////////////////////////////////////
//set motor speed / direction
void engineControl()
{
  if(MOTOR_direction != MOTOR_direction_new) //ramp speed to 0, change direction, ramp speed up
  {
    //change of direction from FWD or RWD
    if((MOTOR_direction==FWD)||(MOTOR_direction==RWD))
    {
      MOTOR_speed -= 5; //ramp down speed

      if(MOTOR_speed<10) //if speed is low enough to stop, change direction
      {
        MOTOR_direction = MOTOR_direction_new;
        currentSenseDeactivate = CURRENT_SENSE_DEACTIVATE_TIME;
      }
      #if DEBUG
        Serial.print("x");
      #endif
    }
    else //change from stop to other direction
    {
      MOTOR_direction = MOTOR_direction_new;
    }
  }
  else if(MOTOR_speed != MOTOR_speed_new) //change in motor speed, without change of direction
  {
    if(MOTOR_speed > MOTOR_speed_new+1) //if actual speed is higher than new speed
    {
      MOTOR_speed -= 2; //ramp down speed

      #if DEBUG
        Serial.print("<");
      #endif
    }
    else if(MOTOR_speed < MOTOR_speed_new-1) //if actual speed is lower than new speed
    {
      MOTOR_speed += 2; //ramp up speed
      #if DEBUG
        Serial.print(">");
      #endif
    }
  }
  else //no change
  {
    MOTOR_speed = MOTOR_speed_new; //just set direction again
  }

  //output speed and direction to motor driver (use one dirction GPIO and one PWM)
  #if MOTOR_L9110
    if(MOTOR_direction == FWD)
    {
      digitalWrite(MOTOR_PIN_DIR, LOW);
      analogWrite(MOTOR_PIN_PWM,MOTOR_speed); //PWM output to motor driver
    }
    else if (MOTOR_direction == RWD)
    {
      digitalWrite(MOTOR_PIN_DIR, HIGH);
      analogWrite(MOTOR_PIN_PWM,255-MOTOR_speed); //PWM inverse output to motor driver
    }
    else
    {
      digitalWrite(MOTOR_PIN_DIR, LOW);
      analogWrite(MOTOR_PIN_PWM,0); //PWM output to motor driver
    }
  #endif

  //output speed and direction to H-Bridge (use two GPIOs and two PWMs)
  #if MOTOR_HBRIDGE
    if(MOTOR_direction == FWD)
    {
      digitalWrite(MOTOR_PIN_GateP_Pos, HIGH); //set Motor-Pos to supply voltage
      digitalWrite(MOTOR_PIN_GateP_Neg, LOW); //disconnect Motor-Neg from supply voltage
      analogWrite(MOTOR_PIN_GateN_Neg,MOTOR_speed); //PWM output to low-side switch on Motor-Neg
      analogWrite(MOTOR_PIN_GateN_Pos,0); //stop PWM output to low-side switch on Motor-Pos
    }
    else if (MOTOR_direction == RWD)
    {
      digitalWrite(MOTOR_PIN_GateP_Neg, HIGH); //set Motor-Neg to supply voltage
      digitalWrite(MOTOR_PIN_GateP_Pos, LOW); //disconnect Motor-Pos from supply voltage
      analogWrite(MOTOR_PIN_GateN_Pos,MOTOR_speed); //PWM output to low-side switch on Motor-Pos
      analogWrite(MOTOR_PIN_GateN_Neg,0); //stop PWM output to low-side switch on Motor-Neg
    }
    else //motor stopped
    {
      digitalWrite(MOTOR_PIN_GateP_Pos, HIGH); //set Motor-Pos to supply voltage  <--- used for start/stop detection
      digitalWrite(MOTOR_PIN_GateP_Neg, LOW); //disconnect Motor-Neg from supply voltage
      analogWrite(MOTOR_PIN_GateN_Neg,0); //stop PWM output to low-side switch on Motor-Neg
      analogWrite(MOTOR_PIN_GateN_Pos,0); //stop PWM output to low-side switch on Motor-Pos
    }
  #endif

}
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
void loop()
{
  loopCount++;
  if(loopCount>1000) //start again at 0 after 10 sec
    loopCount = 0;

  ///////////////////////////////////////////////////////////////////////////////
  //if "PROG" button was pressed: switch to next program
  if(sem_nextProgram)
    incrementProgram();

    if(prog_current != prog_last)
    {
      //currentSet = (prog_current-1)*1000; //max= 5*50=250
      EMK_set = ( prog_current-1)*500;

      //MOTOR_speed = (prog_current-1)*28; //max= 5*50=250

      prog_last = prog_current;
    }


    getMotorData();
    //MotorRegulator(currentSet);
    //MotorRegulatorV(5300);

    //MotorRegulatorEMK(EMK_set);

    //MOTOR_speed=165;
    analogWrite(MOTOR_PIN_PWM,MOTOR_speed); //PWM output to motor driver

   MotorRegulator2(EMK_set);

    if(!(loopCount % 100))
    {
      printSerialData();
    }

    delay(10);
}
*/




/**
 * Divides a given PWM pin frequency by a divisor.
 *
 * The resulting frequency is equal to the base frequency divided by
 * the given divisor:
 *   - Base frequencies:
 *      o The base frequency for pins 3, 9, 10, and 11 is 31250 Hz.
 *      o The base frequency for pins 5 and 6 is 62500 Hz.
 *   - Divisors:
 *      o The divisors available on pins 5, 6, 9 and 10 are: 1, 8, 64,
 *        256, and 1024.
 *      o The divisors available on pins 3 and 11 are: 1, 8, 32, 64,
 *        128, 256, and 1024.
 *
 * PWM frequencies are tied together in pairs of pins. If one in a
 * pair is changed, the other is also changed to match:
 *   - Pins 5 and 6 are paired on timer0
 *   - Pins 9 and 10 are paired on timer1
 *   - Pins 3 and 11 are paired on timer2
 *
 * Note that this function will have side effects on anything else
 * that uses timers:
 *   - Changes on pins 3, 5, 6, or 11 may cause the delay() and
 *     millis() functions to stop working. Other timing-related
 *     functions may also be affected.
 *   - Changes on pins 9 or 10 will cause the Servo library to function
 *     incorrectly.
 *
 * Thanks to macegr of the Arduino forums for his documentation of the
 * PWM frequency divisors. His post can be viewed at:
 *   http://forum.arduino.cc/index.php?topic=16612#msg121031
 */





/*
void printSerialData()
{
  Serial.print("Vp: ");
  Serial.print(MOTOR_MEAS_Vp);
  Serial.print(" Im: ");
  Serial.print(MOTOR_CALC_Im);
  Serial.print("  Vm: ");
  Serial.print(MOTOR_CALC_Vm);
  Serial.print("  Vemk: ");
  Serial.print(MOTOR_CALC_Vemk);
  Serial.print("  n: ");
  Serial.print(MOTOR_CALC_n);
  Serial.print("  PWM: ");
  Serial.println(MOTOR_speed);

  // double MOTOR_MEAS_Vp = 0; //voltage at motor positive connection
  // double MOTOR_MEAS_Vn = 0; //voltage at motor negative connection
  // double MOTOR_MEAS_Vrs = 0; //voltage over current sense resistor
  //
  // //calculated values
  // double MOTOR_CALC_Vm = 0; //voltage at motor connectors
  // double MOTOR_CALC_Im = 0; //current through motor
  // double MOTOR_CALC_Vemk = 0; //generator voltage
  //
  // int MOTOR_CALC_n = 0; //Drehzahl / speed
  // double MOTOR_CALC_M = 0; //Drehmoment / torque
}
*/





///////////////////////////////////////////////////////////////////////////////
//if "START" button was pressed: pause/continue program
/*
if(sem_starStop) //STAR/STOP Button was pressed
{
  //toggle stat_current to stop or continue program
  if(stat_current == STAT_RUN)
  {
    stat_current = STAT_PAUSE;
    MOTOR_speed = MINSPEED;
    #if DEBUG
      Serial.println("status: pause");
    #endif
  }
  else if (stat_current == STAT_PAUSE)
  {
    stat_current = STAT_RUN;
    colorWipe(strip.Color(0, 0, 255), 50); // set all LEDs Red
    #if DEBUG
      Serial.println("status: run");
    #endif
  }

  delay(200);
  sem_starStop = 0; //reset the button press semaphor
}
*/

//setup
/*
#if MOTOR_L293
  pinMode(MOTOR_PIN_DIR1, OUTPUT);
  pinMode(MOTOR_PIN_DIR2, OUTPUT);
  pinMode(MOTOR_PIN_PWM, OUTPUT);

  digitalWrite(MOTOR_PIN_DIR1, LOW);
  digitalWrite(MOTOR_PIN_DIR2, LOW);
  digitalWrite(MOTOR_PIN_PWM, LOW);
#endif

*/


///////////////////////////////////////////////////////////////////////////////
//set motor speed / direction
/*
void engineControl(int newspeed, int dir)
{
  static int old_speed = MINSPEED;
  static int old_dir = 0;

  if(dir != old_dir) //direction changed (or direction and speed changed)
  {
    //change of direction: ramp speed donw -> change direction -> ramp speed up
    engineControlRamp(old_speed, 0); //ramp speed down to zero

    switch (dir)
    {
      case FWD:
        #if MOTOR_L293
          digitalWrite(MOTOR_PIN_DIR1, LOW);
          digitalWrite(MOTOR_PIN_DIR2, HIGH);
        #endif
        #if MOTOR_L9110
          digitalWrite(MOTOR_PIN_DIR, LOW);
        #endif
        engineControlRamp(MINSPEED, newspeed); //ramp speed up from zero to current value
      break;
      case RWD:
        #if MOTOR_L293
          digitalWrite(MOTOR_PIN_DIR1, HIGH);
          digitalWrite(MOTOR_PIN_DIR2, LOW);
        #endif
        #if MOTOR_L9110
          digitalWrite(MOTOR_PIN_DIR, HIGH);
        #endif
        engineControlRamp(MINSPEED, newspeed); //ramp speed up from zero to current value
      break;
      case BREAK:
        #if MOTOR_L293
          digitalWrite(MOTOR_PIN_DIR1, LOW);
          digitalWrite(MOTOR_PIN_DIR2, LOW);
          analogWrite(MOTOR_PIN_PWM,255);
        #endif
        #if MOTOR_L9110
          digitalWrite(MOTOR_PIN_DIR, LOW);
          analogWrite(MOTOR_PIN_PWM,0);
        #endif
      break;
      case FREE:
        #if MOTOR_L293
          analogWrite(MOTOR_PIN_PWM,0);
        #endif
        #if MOTOR_L9110 //freewheel is not possible with L9110: break
          digitalWrite(MOTOR_PIN_DIR, LOW);
          analogWrite(MOTOR_PIN_PWM,0);
        #endif
      break;

    }

  }
  else if (MOTOR_speed_new != MOTOR_speed) //same direction, speed changed
  {
    engineControlRamp(old_speed,newspeed);
  }

  old_speed = newspeed;
  old_dir = dir;
}
*/

///////////////////////////////////////////////////////////////////////////////
//ramp speed from current to new speed to protect the mechanics
/*
void engineControlRamp(int oldSpeed, int newSpeed)
{
    #if DEBUG
      Serial.println("ramp");
    #endif

  int currentSpeed = oldSpeed;

  //increment / decrement speed
  while (newSpeed != currentSpeed)
  {

    if(newSpeed > currentSpeed)
    {
      currentSpeed += SPEEDUP;
      #if DEBUG
        Serial.print(">");
      #endif
    }
    else if(newSpeed < currentSpeed)
    {
      currentSpeed -= SPEEDUP;
     #if DEBUG
      Serial.print("<");
    #endif
    }

    #if MOTOR_L9110
      if(MOTOR_direction == RWD)
      {
        analogWrite(MOTOR_PIN_PWM,255-currentSpeed); //PWM inverse output to motor driver
      }
      else
      {
        analogWrite(MOTOR_PIN_PWM,currentSpeed); //PWM inverse output to motor driver
      }
    #endif
    #if MOTOR_L293
      analogWrite(MOTOR_PIN_PWM,currentSpeed); //PWM output to motor driver
    #endif
    delay(10);
  }

}
*/

///////////////////////////////////////////////////////////////////////////////
//stop motor and show selected program
/*
void pauseProgram()
{
  //engineControl(MINSPEED,FREE);
  //LEDshowProgram();
}
*/
///////////////////////////////////////////////////////////////////////////////
/** This function will be called when "START/STOP" Button is pressed */
/*
void ISRbtnSTART()
{
  //diable interrupts
  sem_starStop = 1;
  delay(1);
  //enable interrupts
}
*/

///////////////////////////////////////////////////////////////////////////////

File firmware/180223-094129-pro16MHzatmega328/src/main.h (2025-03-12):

#include <Arduino.h>
#include <Adafruit_NeoPixel.h>
#include <avr/wdt.h>

/*
https://www.maxonmotor.ch/medias/sys_master/root/8797816094750/maxonMotorData-Handzettel.pdf?attachment=true

https://www.heise.de/select/make/2016/6/1482398401198797
*/

/* Lochraster (013/xx)
//Arduino Mini Pro
//5V, 16MHz quarz
//Onboard 5V/150mA LDO
//Pin 13 (PB5) Onboard green LED (active high)
*/

/* PCB 013/00
5V 8MHz

  [NAME]       [Arduino]   [Atmega]
---------------------------------------
BTN_PIN_PROG      D2      PD2
WS2811_PIN        D9      PB7 rework:PB1
RC_PULLUP_PIN     D0      PD0

MOTOR_PIN...
    _GateP_Neg    D3      PD3
    _GateP_Pos    D4      PD4
    _GateN_Pos    D5      PD5 (OC0B)
    _GateN_Neg    D6      PD6 (OC0A)

ADC_PIN...
    _MOTOR_NEG    A0      PC0 (ADC0)
    _MOTOR_POS    A1      PC1 (ADC1)
    _MOTOR_Rs     A2      PC2 (ADC2)
    _AD_MON_SUP   A3      PC3 (ADC3) (not used)
    _RC           A4      PC4 (ADC4)

*/

//////////////////////////////////////////////////////////////////////////////////////////////////////////
//////////////////////////////////////////////////////////////////////////////////////////////////////////
//RL basic defines
#define INIT_PIN_OUT(ddrx,num)			ddrx |= (1<<num)
#define INIT_PIN_IN(ddrx,num)			ddrx &= ~(1<<num)

#define INIT_PIN_PULLUP(port,num)		port |= (1<<num)
#define INIT_PIN_NO_PULLUP(ddrx,num)	port &= ~(1<<num)

#define SET_PIN_HIGH(port,num)			port |= (1<<num)
#define SET_PIN_LOW(port,num)			port &= ~(1<<num)
#define SET_PIN_TOG(port,num)			port^= (1<<num)

#define PIN_IS_HIGH(pin,num)			pin & (1<<num)
#define PIN_IS_LOW(pin,num)				!(pin & (1<<num))

///////////////////////////////////////////////////////////////////////////////
//system mode
#define BTN_MODE_PAUSE 1  //pause and continue program if "start" button is pressed
#define BTN_MODE_BREAK 0  //stop (go to program PROG_STOP) if "start" button is pressed

///////////////////////////////////////////////////////////////////////////////
/* PIN defines */
//  digital I/Os:
#define BTN_PIN_PROG  2  //switch program

//onboard pullup for RC control
//#define RC_PULLUP_PIN 1  //PD1 GPIO1
#define RC_PULLUP_PIN 0 //REWORK 09-06-2020: use RXD pin to control pull-up

//  Motor control:
#if MOTOR_HBRIDGE
  #define MOTOR_PIN_PWM   9  //
  #define MOTOR_PIN_DIR1  12   //
  #define MOTOR_PIN_DIR2  11  //

  #define MOTOR_PIN_GateP_Neg   3 //PD3
  #define MOTOR_PIN_GateP_Pos   4 //PD4
  #define MOTOR_PIN_GateN_Pos   5 //PD5 PWM (OC0B)
  #define MOTOR_PIN_GateN_Neg   6 //PD6 PWM (OC0A)

  #define ADC_PIN_MOTOR_POS 1
  #define ADC_PIN_MOTOR_NEG 0
#endif

//  analog inputs:
//Motor current sense
#define ADC_PIN_MOTOR_Rs 2 //PC2 ADC2

//Remote Control
//#define ADC_PIN_RC  5     //PC5 ADC5
#define ADC_PIN_RC  4     //PC4 ADC4 RXD //REWORK 09-06-2020:

//Supply voltage measurement
#define ADC_PIN_MON_SUP  3     //PC3 ADC3


///////////////////////////////////////////////////////////////////////////////
//increase speed in prog "speed up"
#define SPEEDUP 1
///////////////////////////////////////////////////////////////////////////////
//control bits (button press...)
unsigned char sem_nextProgram = 0;  //is set to 1 if PROG button is pressed
unsigned char sem_starStop = 0;     //is set to 1 if START button is pressed
///////////////////////////////////////////////////////////////////////////////
//list of all available programs
#define MAX_PROGRAM 5

#define PROG_NORMAL   1
#define PROG_SPEEDUP  2
#define PROG_CRACY    3
#define PROG_MAXSPEED 4
#define PROG_RC       5

unsigned char prog_current = 1;	//current selected Programm
///////////////////////////////////////////////////////////////////////////////
//list of all program status
#define STAT_PAUSE  0
#define STAT_RUN    1
#define STAT_STOP   3

unsigned char stat_current = 0;  //1: stat_current/continue program, 0: program is stopped
///////////////////////////////////////////////////////////////////////////////
//Motor speed (140->255)

//Vin=7.5V SPEED_CORRECTION_FACTOR = 1
//Vin= 12V SPEED_CORRECTION_FACTOR = 0.6
#define SPEED_CORRECTION_FACTOR 1

#define ABSMINSPEED (20 * SPEED_CORRECTION_FACTOR)
#define MINSPEED  (70  * SPEED_CORRECTION_FACTOR)//with a lower value the motor will not move
#define NORMSPEED (70 * SPEED_CORRECTION_FACTOR)//70
#define MAXSPEED  (255 * SPEED_CORRECTION_FACTOR)

unsigned char MOTOR_speed = 0;	//
unsigned char MOTOR_speed_new = 0;
///////////////////////////////////////////////////////////////////////////////
//motor direction
#define STOP  0
#define RWD   1	//backward
#define FWD   2	//forward
#define BREAK 3	//break
#define FREE  4	//freewheel

unsigned char MOTOR_direction = 0;	//motor dir
unsigned char MOTOR_direction_new = 0;	//motor dir
///////////////////////////////////////////////////////////////////////////////
unsigned char PWM_val = 255;	//aktuelle PWM OFF Zeit
unsigned char LED_speed = MINSPEED;
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

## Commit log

2022-10-27 setup project structure
    [LoopingLouino.kicad_pcb]
2025-03-12 add new KiCAD files
    add information on how to flash the bootloader
    [BOM-0 013-00.xlsx, LoopingLouino.kicad_pcb, LoopingLouino.kicad_sch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]
2025-03-14 use 20 LEDs
